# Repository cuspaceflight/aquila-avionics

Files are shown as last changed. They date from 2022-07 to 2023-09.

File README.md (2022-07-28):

# Aquila Avionics
Schematics and firmware for Aquila flight computer.

## Functions
* **Altimetry** - Accurately estimate altitude with barometer, GPS and accelerometer
* **Recovery** - Activate pyrotechnics to deploy parachute stages at appropriate points during descent
*  **Data logging** - Log altitude data and other parameters for post-flight analysis
* **Telemetry** - Transmit data to a ground station during flight as a backup should the vehicle be lost
* **Location** - Continually transmit location after landing to aid finding the vehicle

## Specifications
* **Mass** -  2kg
* **Acceleration** - 30g
* **Altitude** - 150km
* **Speed** - 1500m/s
* **Flexibility** - Exact flight and recovery profile is TBC
*  **Budget** - �150

# Overview
What follows here is a very brief overview of the design, broken down by component. It's aim is to familiarise the reader with what this project includes and some of the decisions made.
## Batteries
The computer is designed to run from two 18650 Li-Ions in series. A battery management chip monitors the cell voltages and automatically balances them if necessary. There is no onboard charger, so batteries must be charged separately before installation/flights. Ideally cells with built-in under-volt protection should be used. The battery holders are physically mounted to the board (but will be mechanically supported by additional hardware). Power can be switched on and off via a screw terminal.  To connect the batteries to the rest of the board, a jumper is secured between the two terminals. A potential divider allows the microcontroller to directly monitor the battery voltages.

Additionally, a 3V CR2032 type cell is mounted to the board. This maintains real time clocks in the microcontroller and GPS receiver, improving resilience against power cycle events during flight.
## Power supplies
The board has two power supplies: 3.3V 3A and 5V 3A. The 3.3V supply powers most of the electronics on the board and is permanently on. The 5V supply is dedicated to pyrotechnics and servos as required by the recovery system. It is switched on and off by the microcontroller to conserve power when not needed and as a safety layer. A terminal is provided for an external safety switch. When shorted, this terminal disables the pyro power supply, eliminating the risk of unintentionally activating pyrotechnics during any activities leading up to launch.
## Sensors
### Barometer
A barometer is mounted on the board to measure atmospheric pressure. This is particularly useful during descent to deploy parachute stages at appropriate altitudes close to the ground. The model used is a MS5611-01BA03. It has a resolution on the order of tenths of millibar, but a minimum pressure of 10 millibar limits it's usefulness to below 30 km altitude.
### GPS
A U-blox MAX-M8Q receiver is included for completeness. CoCom regulations limit the operation of civilian GPS chips faster than 1000 knots (~500 m/s) and above 18 km, both of which will be exceeded early in Griffin's flight profile. Therefore the GPS will not be relied on for navigational purposes, but purely for data collection. It may be the case that once the rocket slows below 1000 knots near apogee, a fix can once again be acquired. This is uncertain as the manufacturer does not specify behaviour at these extremes.

An additional Low-Noise Amplifier and band-pass filter are included in the signal path as antenna challenges and telemetry radio interference will degrade signal quality.
### Accelerometer
The most important sensor for navigation and apogee deployment is the accelerometer. An inertial navigation system will be implemented to estimate the vehicle's velocity and altitude based on accelerometer readings. The double integration of acceleration to velocity leads to errors on the order of time squared, so it is imperative the accelerometer readings are low noise and very stable. Combined with this requirement, a high g range is required as the rocket will accelerate at up to 30g at some points.  An Analog Devices ADXL357 is chosen. It boasts 20 bit resolution, ultra-low noise and high bias stability with a range of +/- 40g.
## Telemetry
An Si4463 radio transceiver provides a bi-directional radio link with a ground station. This will be useful for configuring the computer during launch preparations as well as backing up as much data as possible should the vehicle be lost. A secondary purpose for the radio will be locating the vehicle after a successful recovery. The current setup is designed for operation in the 915 MHz ISM band, subject to regulatory compliance.
## Interfaces
Connectors on the board include: 
* **female SMA** for GPS antenna
* **female SMA** for telemetry antenna
* **6-way Molex Nano-Fit** for a separate, remote, barometer, in case structural limitations prevent the avionics bay being vented to the atmosphere
* **6-way Molex Nano-Fit** for up to four servo motors
* **4x 2-way screw terminal** for up to four pyrotechnics
* **Micro USB** for programming and serial communication

The pyro channels can provide 5V at 1A continuous as limited by the FETs, 3A peak as limited by the power supply. They also include individual continuity measurement by draining approximately 50uA through the pyro.
## Microcontroller
A Teensy 4.1 was selected as the microcontroller. It is based around an ARM Cortex-M7 running at 600MHz. The first reason for this choice is that it includes many features we would only have to implement ourselves such as a real time clock, MicroSD storage, USB interface etc. Secondly, it is compatible with the Arduino ecosystem, granting access to many existing libraries and improving access to the firmware for CUSF members.
## Antennas
Antennas are an area of ongoing research, hence nothing has been included in this repo yet. Carbon-fibre reinforced polymer (CFRP) construction precludes antennas being mounted inside the rocket body, and extreme aerodynamic and aerothermal loads make any kind of protruding antenna impossible. This leaves the only possible solution as conformal patch antenna arrays. Methods to design and optimise these antennas and feed networks are currently being developed. See <https://github.com/cuspaceflight/aperture>.

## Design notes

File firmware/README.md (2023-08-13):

#### Important:
Copy the `aquila_interface` folder into your `Arduino/libraries` directory before compiling. If you wish to run Hardware-In-Loop (HIL) testing, also copy `aquila_hil_interface.h` and `aquila_hil_interface.cpp` into this libraries folder.

#### Guide to files
* aquila_flight - actual flight program
* aquila_interface - library for interacting with Aquila hardware
* individual_sensor_tests - a small program for each sensor, used to test protocols
* inertial_calibration - calculates two-point calibrations for accelerometers and gyroscopes by having you hold the board in different orientations
* sensor_dump - reads all sensors using aquila_interface and prints their values to serial

#### HIL Testing
To run an HIL test on the flight computer with imitated sensor readings from a simulated flight, uncomment the indicated line at the top of `aquila_flight.ino`. The "liftoff" will occur automatically 30 seconds after startup, so make sure to issue the "unlock" command within this time.

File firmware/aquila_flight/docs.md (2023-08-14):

# Aquila Flight Software Documentation

## Contents

**Requirement-to-Code Tracking**

**Hardware Interface**

**Design**

- System States
- Background Operations
- Serial Interface

## Requirement-to-Code Tracking

To ensure the software meets all high-level requirements and does not contain any unused code, sections of the requirements are linked to sections of the source code. These are indicated by square brackets containing a number. The source code is commented with corresponding numbers to indicate where these requirements are implemented. For example a requirement may say “When X is true, Y should occur \[42]” and the corresponding section of code will have a comment “// REQ\[42]”. Where a single section of code serves to implement several requirements, the comment contains all of them e.g. “// REQ\[42]\[45]\[51]”. These should be standalone comments at the beginning of blocks of code or at the end of specific lines.

## Hardware Interface

A library called ‘aquila\_interface’ has been written to interface with the sensors and peripherals on the board. This is bare-bones protocol level code, and does not have a set of formal requirements associated with it at this time.

## High-Level Requirements

The architecture of the Aquila Flight program comprises two types of code: mode based; and background. The system state represents the current stage of flight, with transitions occurring when specific conditions are met. The transition from one mode to another may be associated with one or more actions such as actuation of a vehicle system. Background functions are run repeatedly at set rates to update sensor readings or log data. Some background functions may run only when the system is in specific modes.

### System States

There are seven total flight stages, represented by a mode. \[1]

| **Num** | **Name** | **Criteria to enter** | **Actions** |
| --- | --- | --- | --- |
| 0 | LOCKED | Startup \[2], lock command received \[45] | Set altitude and velocity estimates to zero \[46] |
| 1 | PAD | unlock command received \[3] | |
| 2 | BURN | velocity > 10m/s \[4] | |
| 3 | COAST | acceleration < 0 \[5] | |
| 4 | APOGEE | velocity < 0 \[6] | Activate bottle burst pyro \[9] |
| 5 | DESCENT  | barometric altitude below 500m \[7] | Release parachute servos \[10] |
| 6 | LAND | Barometric pressure constant for 10 seconds \[8] | Reduce logging rate to 10Hz \[11], disarm pyros \[51] |

### Background Operations

| **Operation** | **Modes** | **Rate** | **Description** |
| --- | --- | --- | --- |
| Acceleration integration | all except LOCKED and LAND \[18] | \~1kHz\[24] | The ADXL357 raises an interrupt when it has a new reading. The handler updates the velocity and altitude estimates \[30]. When in PAD state, accelerations < 0.01g are discarded \[47]. |
| Sensor updates | All \[19] | 100Hz \[25] | All sensors are read and readings stored \[31] |
| Data logging | All \[20] | 100Hz\[26]  | Write all sensor readings and system parameters to SD card \[32] |
| Telemetry transmission | All \[21] | 10Hz\[27] | Transmit packet of sensor readings and system parameters over radio \[33] |
| Telecommand reception  | All \[21] | 10Hz\[27] | Receive command from radio \[52] |
| Serial write | LOCKED and PAD \[22] | 10Hz\[28] | Send sensor readings and system parameters over Serial \[34] |
| Serial read | LOCKED and PAD \[23] | 100Hz\[29]  | Read serial port for commands \[35] |

### Command Interface

Several commands can be sent to the vehicle either by the serial connection or via the radio. The commands currently implemented are as follows.

| **Command** | **Action** |
| --- | --- |
| N | Print system state to console \[36] |
| S | Start printing system state at a rate of 10Hz \[37] |
| P | Stop printing system state \[38] |
| L | Put system into LOCKED state and reset altitude and velocity \[39] |
| U | Put system into PAD state \[40] |
| V\* | Toggle servo position - LOCKED state only \[41] |
| A | Arm pyrotechnics \[42] |
| D | Disarm pyrotechnics \[43] |
| C | Calibrate launch pad barometric pressure \[49] |

\* requires pyrotechnics to be armed \[44]

### Recovery Safety

To prevent unintentional release of the spring loaded recovery system, the servos should be set to the latched position whenever the pyro channels are armed \[48].

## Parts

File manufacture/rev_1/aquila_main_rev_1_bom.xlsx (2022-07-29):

Item | Qty | Reference(s) | Value | LibPart | Footprint | Datasheet | DigiKey | Farnell | Mouser | RS
1 | 3 | C1, C2, C20 | 100p | aquila:C-cusf-kicad | Capacitor_SMD:C_0402_1005Metric |  |  | 1758969
2 | 3 | C3, C4, C18 | 100n | aquila:C-cusf-kicad | Capacitor_SMD:C_0402_1005Metric |  |  | 2320759
3 | 2 | C5, C6 | 22u | aquila:C-cusf-kicad | Capacitor_THT:CP_Radial_D6.3mm_P2.50mm |  |  | 9452710
4 | 2 | C7, C8 | 1u | aquila:C-cusf-kicad | Capacitor_SMD:C_0402_1005Metric |  |  | 2310531
5 | 2 | C9, C10 | 1000u | Device:C_Polarized_Small | Capacitor_THT:CP_Radial_D8.0mm_P3.50mm | https://www.farnell.com/datasheets/2820375.pdf |  | 2760327
6 | 1 | C11 | 3p | Strix:C | Capacitor_SMD:C_0402_1005Metric |  |  | 1758933
7 | 1 | C12 | 5p1 | Strix:C | Capacitor_SMD:C_0402_1005Metric |  |  | 2781439
8 | 1 | C13 | 1p2 | Strix:C | Capacitor_SMD:C_0402_1005Metric |  |  | 3369062
9 | 9 | C14, C16, C22, C23, C27, C28, C30, C32, C35 | 0u1 | aquila:C-cusf-kicad | Capacitor_SMD:C_0402_1005Metric |  |  | 2320759
10 | 1 | C15 | 6n8 | Strix:C | Capacitor_SMD:C_0402_1005Metric |  |  | 2627370
11 | 5 | C17, C29, C31, C33, C36 | 10u | aquila:C-cusf-kicad | Capacitor_SMD:C_0402_1005Metric |  |  | 3013332
12 | 2 | C19, C26 | 20p | aquila:C-cusf-kicad | Capacitor_SMD:C_0402_1005Metric |  |  | 1758948
13 | 2 | C21, C24 | 3p3 | Strix:C | Capacitor_SMD:C_0402_1005Metric |  |  | 2627406
14 | 1 | C25 | 0u33 | aquila:C-cusf-kicad | Capacitor_SMD:C_0402_1005Metric |  |  | 2627379
15 | 1 | C34 | 10n | aquila:C-cusf-kicad | Capacitor_SMD:C_0402_1005Metric |  |  | 1758926
16 | 1 | C37 | 2n2 | aquila:C-cusf-kicad | Capacitor_SMD:C_0402_1005Metric |  |  | 2320767
17 | 2 | D1, D2 | 1N5820 | Diode:1N5820 | Diode_THT:D_DO-201AD_P15.24mm_Horizontal | http://www.vishay.com/docs/88526/1n5820.pdf |  | 2317410
18 | 1 | D3 | GREEN | Device:LED_Small | Diode_SMD:D_0603_1608Metric | ~ |  | 3796304
19 | 1 | D4 | RED | Device:LED_Small | Diode_SMD:D_0603_1608Metric | ~ |  | 3796306
20 | 2 | D5, D6 | D_TVS | aquila:D_TVS | Diode_SMD:D_0402_1005Metric |  |  | 2368169
21 | 10 | H1, H2, H3, H4, H5, H6, H7, H8, H9, H10 | M3 | Mechanical:MountingHole_Pad | MountingHole:MountingHole_3.2mm_M3_DIN965_Pad | ~
22 | 1 | IC1 | MS5611-01BA03 | aquila:MS5611-01BA03 | aquila:MS5611 |  |  | 2362662
23 | 1 | J1 | 120591-1 | aquila:120591-1 | aquila:120591-1 | https://www.farnell.com/cad/1815976.pdf | A99328-ND
24 | 2 | J2, J3 | 1042 | aquila:1043P | aquila:1042 |  | 36-1042P-ND
25 | 1 | J4 | PWR | Connector:Screw_Terminal_01x02 | aquila:MP_2.54_screw_terminal_2x1 | ~ |  | 3817460
26 | 1 | J5 | TELEM | Connector:Conn_Coaxial | aquila:SMA_VERT | https://www.mouser.co.uk/datasheet/2/398/PCB.SMAFST.J.A.HT-26997.pdf |  |  | 960-PCB.SMAFST.J.AHT
27 | 1 | J6 | GPS | Connector:Conn_Coaxial | aquila:SMA_VERT | https://www.mouser.co.uk/datasheet/2/398/PCB.SMAFST.J.A.HT-26997.pdf |  |  | 960-PCB.SMAFST.J.AHT
28 | 1 | J7 | BARO | Connector:Conn_01x06_Male | aquila:molex_nano_fit_x6_105310-1106 | https://www.molex.com/pdm_docs/sd/1053101106_sd.pdf | WM16880-ND | 2820682
29 | 1 | J8 | BMI-S-201 | aquila:BMI-S-201 | aquila:BMI-S-201 | ~ |  | 2497715 | ~ | ~
30 | 1 | J9 | PYRO_1 | Connector:Screw_Terminal_01x02 | aquila:MP_2.54_screw_terminal_2x1 | ~ |  | 3817460
31 | 1 | J10 | PYRO_3 | Connector:Screw_Terminal_01x02 | aquila:MP_2.54_screw_terminal_2x1 | ~ |  | 3817460
32 | 1 | J11 | PYRO_2 | Connector:Screw_Terminal_01x02 | aquila:MP_2.54_screw_terminal_2x1 | ~ |  | 3817460
33 | 1 | J12 | PYRO_4 | Connector:Screw_Terminal_01x02 | aquila:MP_2.54_screw_terminal_2x1 | ~ |  | 3817460
34 | 1 | J13 | PYRO_SAFE | Connector:Screw_Terminal_01x02 | aquila:MP_2.54_screw_terminal_2x1 | ~ |  | 3817460
35 | 1 | J14 | SERVO | Connector:Conn_01x06_Male | aquila:molex_nano_fit_x6_105310-1106 | https://www.molex.com/pdm_docs/sd/1053101106_sd.pdf | WM16880-ND | 2820682
36 | 2 | L1, L2 | 100u | aquila:L-cusf-kicad | aquila:L_MP0028_124_125_127 | https://www.farnell.com/datasheets/3486014.pdf |  | 2288307
37 | 1 | L3 | 120n | Strix:L | Inductor_SMD:L_0402_1005Metric |  |  | 3471254
38 | 1 | L4 | 18n | Strix:L | Inductor_SMD:L_0402_1005Metric |  |  | 1343084
39 | 1 | L5 | 3n3 | Strix:L | Inductor_SMD:L_0402_1005Metric |  |  | 1343068
40 | 2 | L6, L8 | 24n | Strix:L | Inductor_SMD:L_0402_1005Metric |  |  | 3263549
41 | 2 | L7, L9 | 12n | Strix:L | Inductor_SMD:L_0402_1005Metric |  |  | 1343082
42 | 2 | NT1, NT2 | Tie_2 | Device:NetTie_2 | NetTie:NetTie-2_THT_Pad1.0mm | ~
43 | 1 | NT3 | NetTie_2 | Device:NetTie_2 | NetTie:NetTie-2_SMD_Pad0.5mm | ~
44 | 4 | Q1, Q2, Q3, Q4 | IRF7509PbF | :IRF7509PbF_6 | aquila:IRF7509PbF | https://www.farnell.com/datasheets/138074.pdf |  | 1611421
45 | 10 | R1, R22, R23, R24, R25, R26, R33, R34, R35, R36 | 10k | aquila:R-cusf-kicad | Resistor_SMD:R_0402_1005Metric |  |  | 2072517
46 | 8 | R2, R6, R7, R9, R15, R16, R19, R20 | DNP | aquila:R-cusf-kicad | Resistor_SMD:R_0402_1005Metric
47 | 4 | R3, R12, R13, R14 | 100 | aquila:R-cusf-kicad | Resistor_SMD:R_0402_1005Metric |  |  | 2072515
48 | 1 | R4 | 330 | aquila:R-cusf-kicad | Resistor_SMD:R_0402_1005Metric |  |  | 2074057
49 | 4 | R5, R8, R17, R18 | 0 | aquila:R-cusf-kicad | Resistor_SMD:R_0402_1005Metric
50 | 2 | R10, R11 | 160 | aquila:R-cusf-kicad | Resistor_SMD:R_0402_1005Metric |  |  | 2072673
51 | 1 | R21 | 20k | aquila:R-cusf-kicad | Resistor_SMD:R_0402_1005Metric |  |  | 2072753
52 | 8 | R27, R28, R29, R30, R39, R40, R41, R42 | 100k | aquila:R-cusf-kicad | Resistor_SMD:R_0402_1005Metric |  |  | 2072519
53 | 4 | R31, R32, R43, R44 | 200k | aquila:R-cusf-kicad | Resistor_SMD:R_0402_1005Metric |  |  | 2072758
54 | 3 | R37, R38, R45 | 4k7 | aquila:R-cusf-kicad | Resistor_SMD:R_0402_1005Metric |  |  | 2073064
55 | 35 | TP1, TP2, TP3, TP4, TP5, TP6, TP7, TP8, TP9, TP10, TP11, TP12, TP13, TP14, TP15, TP16, TP17, TP18, TP19, TP20, TP21, TP22, TP23, TP24, TP25, TP26, TP27, TP28, TP29, TP30, TP31, TP32, TP33, TP34, TP35 | TestPoint | Connector:TestPoint | TestPoint:TestPoint_Pad_D1.0mm | ~
56 | 1 | U1 | LM2576S-3.3/NOPB | aquila:LM2576S-3.3{slash}NOPB | aquila:TO-236_5 | https://www.ti.com/lit/ds/symlink/lm2576.pdf |  | 3008143
57 | 1 | U2 | LM2576D2TR4-5G | aquila:LM2576S-3.3{slash}NOPB | aquila:TO-236_5 | https://www.farnell.com/datasheets/5904.pdf |  | 2534166
58 | 1 | U3 | MAX-M8Q | RF_GPS:MAX-M8Q | aquila:MAX-M8Q | https://www.u-blox.com/sites/default/files/MAX-M8-FW3_DataSheet_%28UBX-15031506%29.pdf
59 | 1 | U4 | Si4463 | RF:Si4463 | Package_DFN_QFN:QFN-20-1EP_4x4mm_P0.5mm_EP2.6x2.6mm_ThermalVias | https://www.silabs.com/documents/public/data-sheets/Si4464-63-61-60.pdf | 336-4346-1-ND
60 | 1 | U5 | B3520 | aquila:B3520 | aquila:B3520 | https://media.digikey.com/pdf/Data%20Sheets/Epcos%20PDFs/B39162B3520U410.pdf | 495-2363-1-ND
61 | 1 | U6 | SKY65723-11 | aquila:SKY65723-11 | aquila:SKY65723-81 | https://www.skyworksinc.com/-/media/SkyWorks/Documents/Products/2801-2900/SKY65723_11_203921F.pdf |  |  | 873-SKY65723-81
62 | 1 | U7 | ADXL357 | aquila:ADXL357 | aquila:ADXL357 |  | 505-ADXL357BEZ-ND
63 | 1 | U8 | BQ29200 | aquila:BQ29200 | aquila:VSOP-8 | https://www.ti.com/lit/ds/symlink/bq29200.pdf?ts=1647814951091 |  | 2383074
64 | 1 | U9 | Teensy4.1 | teensy:Teensy4.1 | teensy:Teensy41 |  | 223-1622-1-ND
65 | 1 | U10 | MPU-6050 | Sensor_Motion:MPU-6050 | Sensor_Motion:InvenSense_QFN-24_4x4mm_P0.5mm | https://store.invensense.com/datasheets/invensense/MPU-6050_DataSheet_V3%204.pdf |  | 3769961
66 | 1 | Y1 | 30M | Device:Crystal_GND2_Small | aquila:crystal_ABM8 | https://www.farnell.com/datasheets/2792510.pdf |  | 3228351

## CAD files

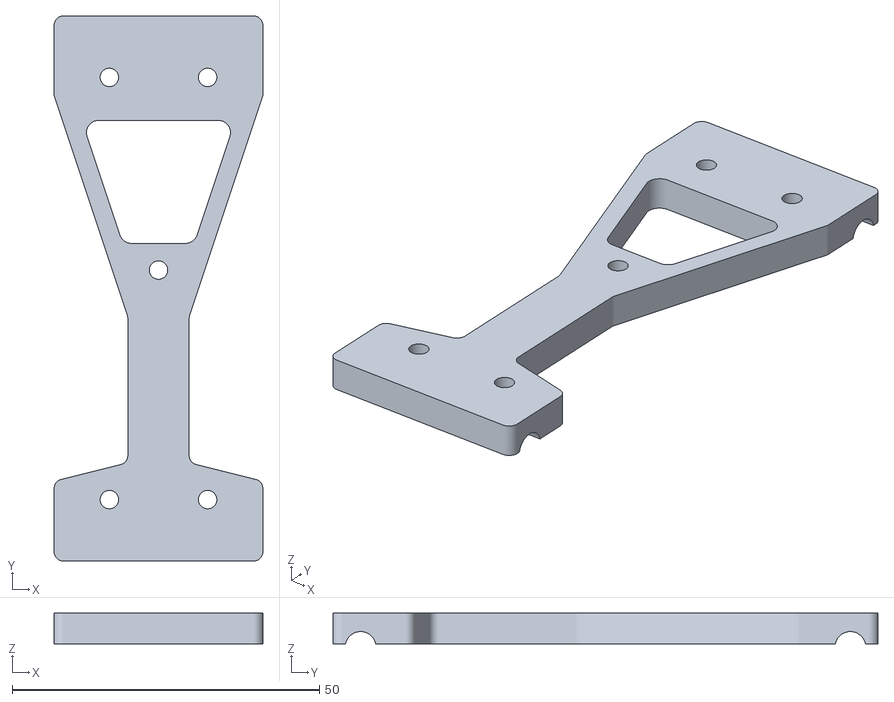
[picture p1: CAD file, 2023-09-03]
mounting/rfm95w_mount-top.stl
34.0 x 88.8 x 5.00

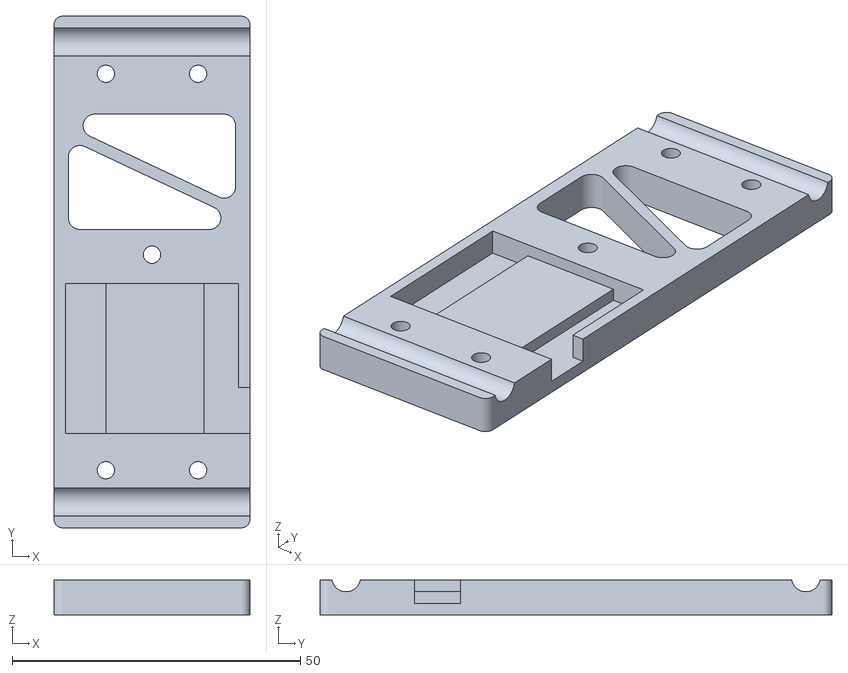
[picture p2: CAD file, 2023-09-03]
mounting/rfm95w_mount-base.stl
34.0 x 88.8 x 6.00

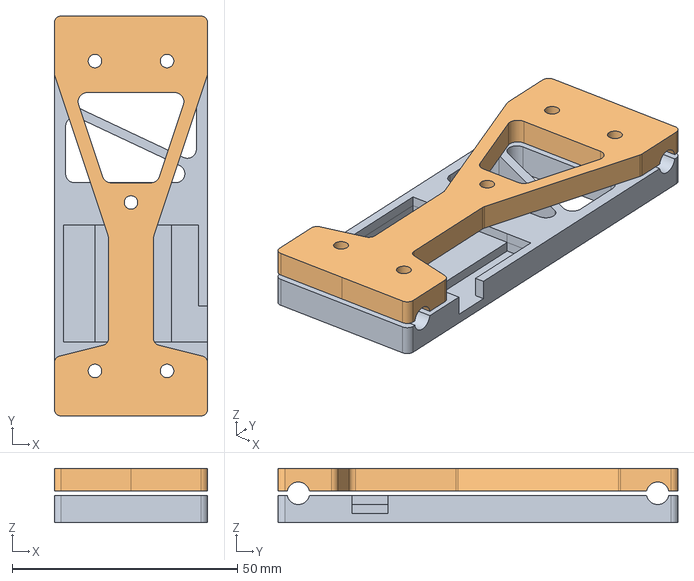
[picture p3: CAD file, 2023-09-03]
mounting/rfm95w_mount.FCStd
34.0 x 88.8 x 12.0 mm

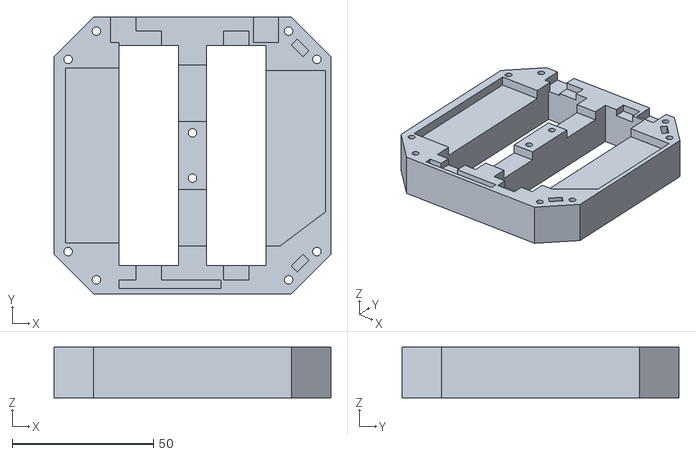
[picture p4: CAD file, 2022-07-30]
mounting/support-PartBody.stl
98.0 x 98.0 x 18.0

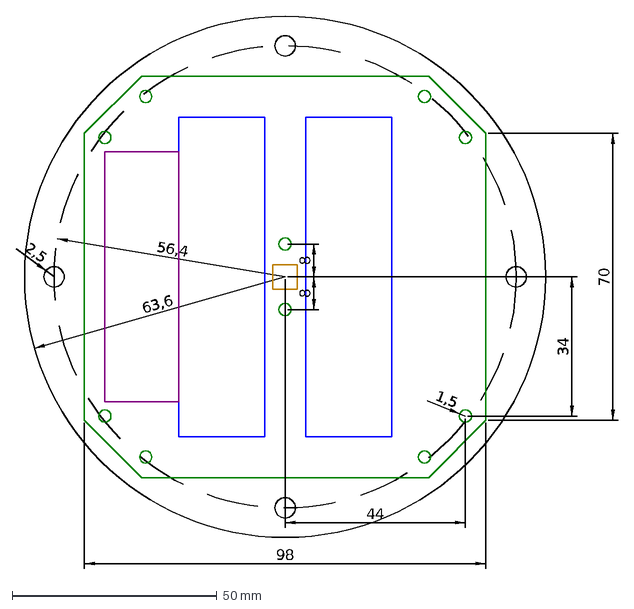
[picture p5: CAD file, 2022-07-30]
mounting/#flange.dxf
63,6
56,4
98
70
2,5
8
44
34
1,5

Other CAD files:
mounting/support.FCStd
mounting/flange.dxf

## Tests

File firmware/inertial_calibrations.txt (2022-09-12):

----- ADXL357 -----
x sensitivity: 12535.15
x offset: 64.44
y sensitivity: 12622.60
y offset: 163.36
z sensitivity: 12157.37
z offset: 1270.68
----- MPU6050 Acceleromter -----
x sensitivity: 2045.54
x offset: 147.62
y sensitivity: 2048.25
y offset: -31.73
z sensitivity: 2099.57
z offset: -51.80
----- MPU6050 Gyroscopes -----
x offset: -51.39
y offset: -21.91
z offset: 1.77
All offsets in LSB, accelerometer sensitivities in LSB /g

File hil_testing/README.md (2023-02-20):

#### HIL Testing
These files are used to generate code for HIL testing. The CSV file contains data from a flight simulation by B. Wardell: https://github.com/Barty129/Uncarved-Block/. The Python program converts this data to an interpolating function in C++ code, so that it can be directly pasted into aquila_hil_interface.cpp.

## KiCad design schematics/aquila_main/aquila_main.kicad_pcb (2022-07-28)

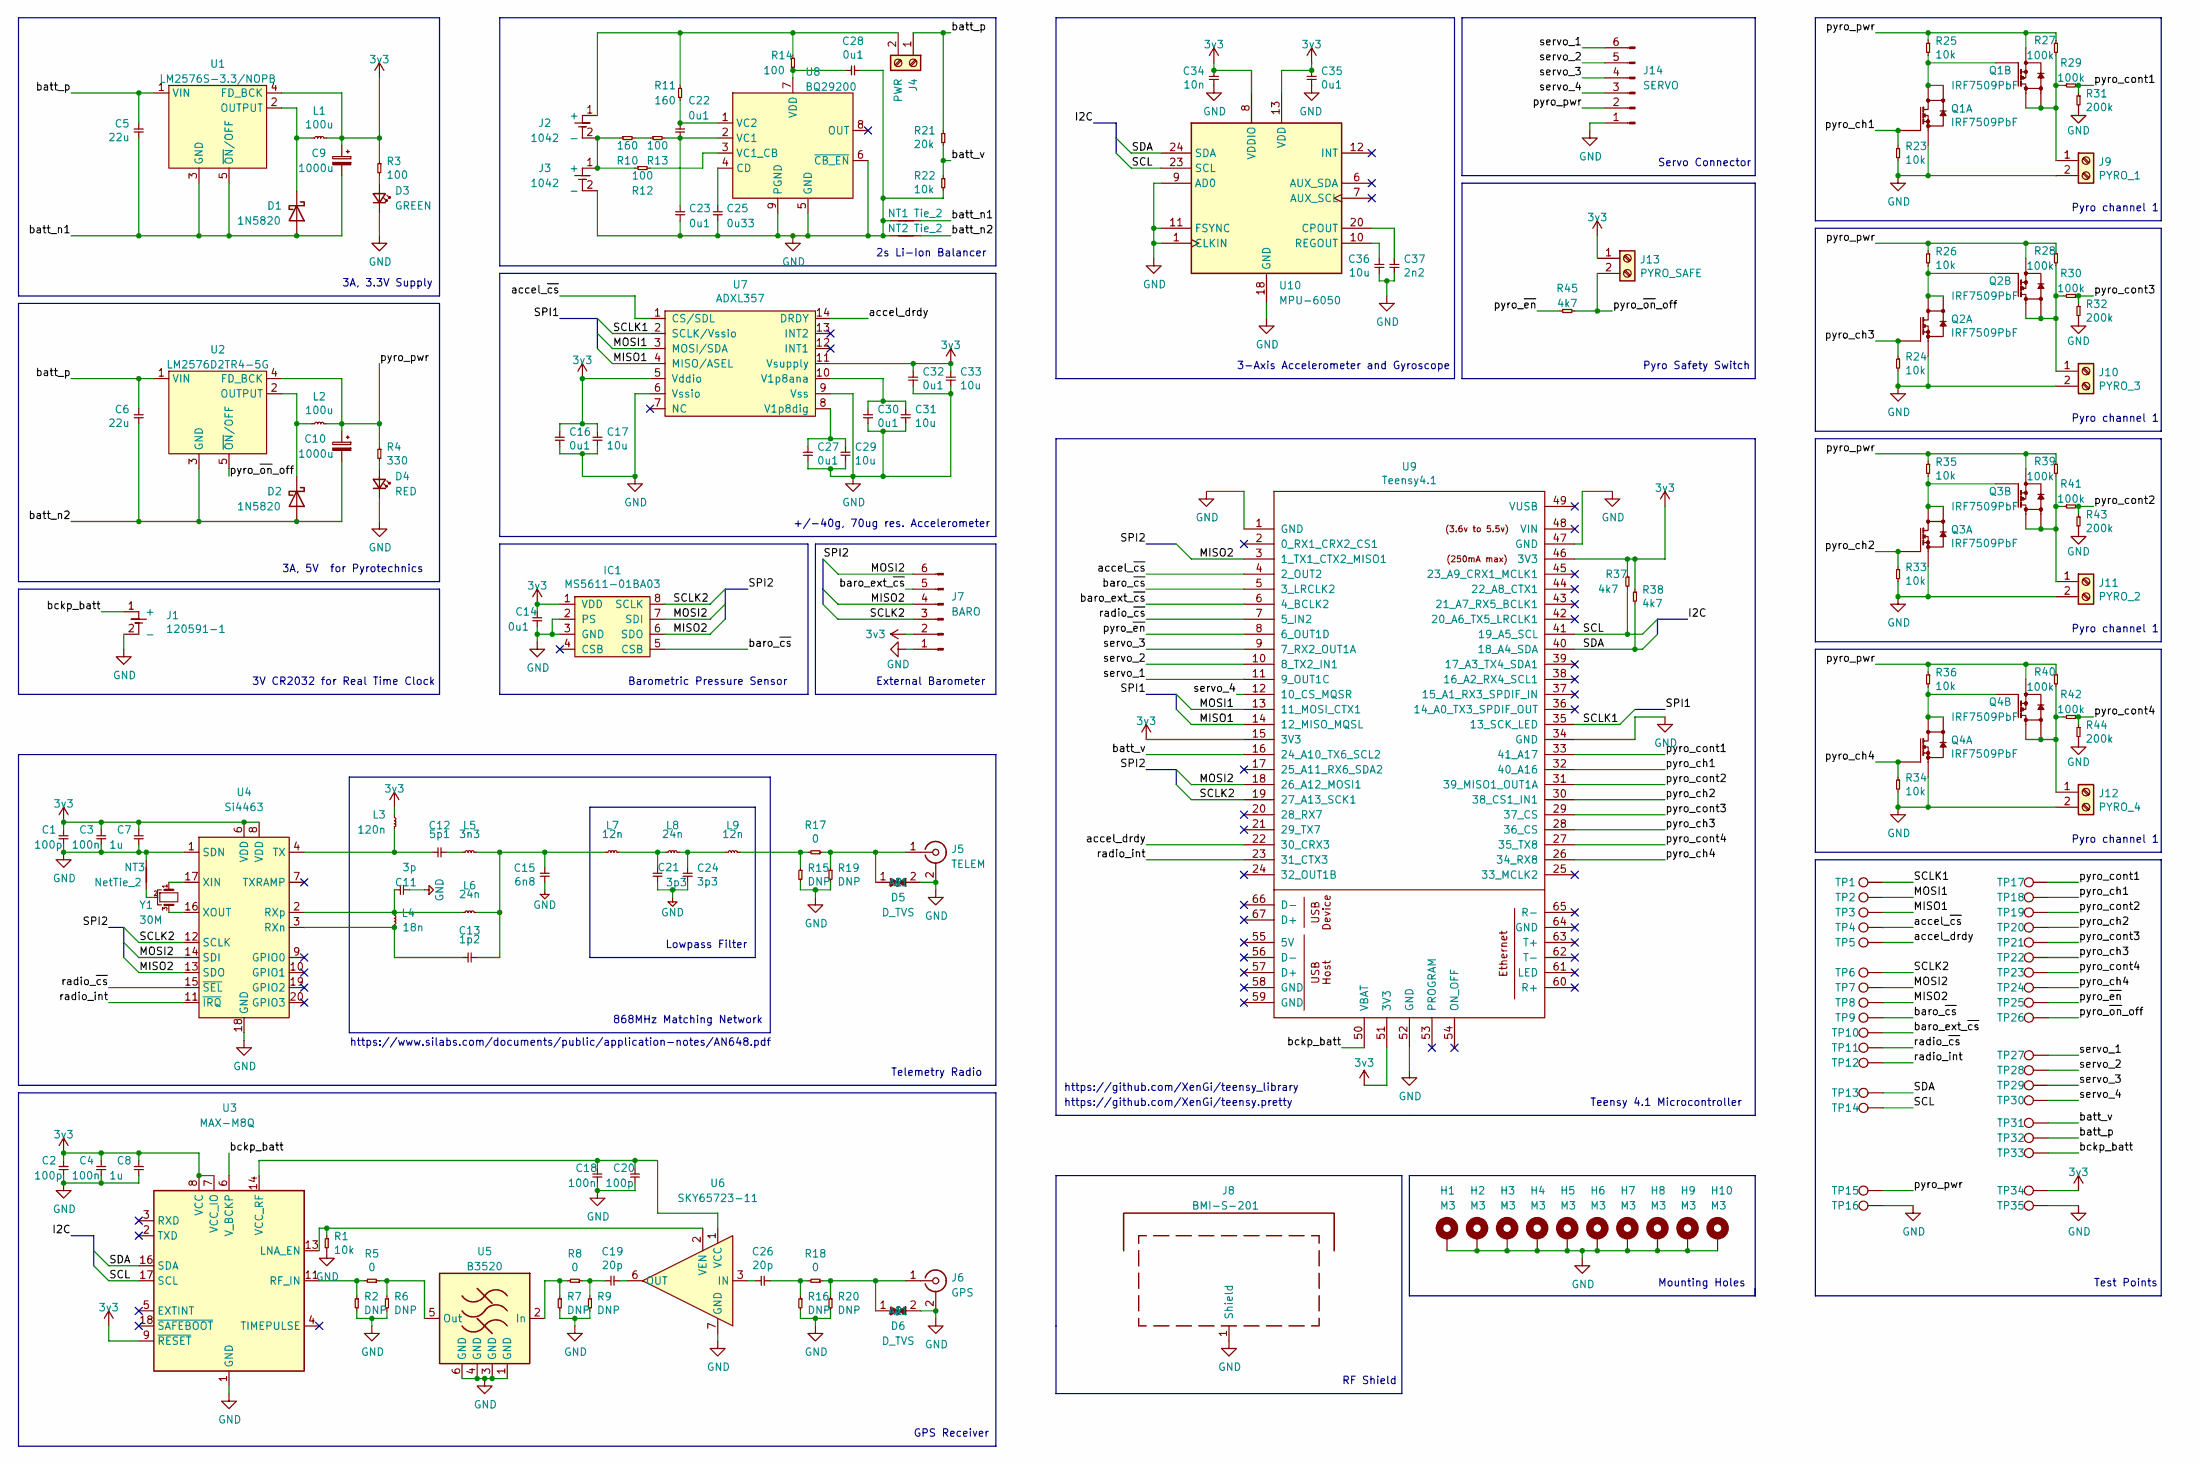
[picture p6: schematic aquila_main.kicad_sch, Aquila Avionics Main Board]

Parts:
C1, C2, C20: 100p; C_0402_1005Metric
C3, C4, C18: 100n; C_0402_1005Metric
C5, C6: 22u; CP_Radial_D6.3mm_P2.50mm; Farnell 9452710
C7, C8: 1u; C_0402_1005Metric
C9, C10: 1000u; CP_Radial_D8.0mm_P3.50mm; Farnell 2760327
C11: 3p; C_0402_1005Metric; Farnell 1758933
C12: 5p1; C_0402_1005Metric; Farnell 2781439
C13: 1p2; C_0402_1005Metric; Farnell 3369062
C14, C16, C22, C23, C27, C28, C30, C32, C35: 0u1; C_0402_1005Metric
C15: 6n8; C_0402_1005Metric; Farnell 2627370
C17, C29, C31, C33, C36: 10u; C_0402_1005Metric
C19, C26: 20p; C_0402_1005Metric
C21, C24: 3p3; C_0402_1005Metric; Farnell 2627406
C25: 0u33; C_0402_1005Metric
C34: 10n; C_0402_1005Metric
C37: 2n2; C_0402_1005Metric
D1, D2: 1N5820; D_DO-201AD_P15.24mm_Horizontal; Farnell 2317410
D3: GREEN; D_0603_1608Metric; Farnell 3796304
D4: RED; D_0603_1608Metric; Farnell 3796306
D5, D6: D_TVS; D_0402_1005Metric; Farnell 2368169
H1, H2, H3, H4, H5, H6, H7, H8, H9, H10: M3; MountingHole_3.2mm_M3_DIN965_Pad
IC1: MS5611-01BA03; MS5611; Farnell 2362662
J1: 120591-1; DigiKey A99328-ND
J2, J3: 1042; DigiKey 36-1042P-ND
J4: PWR; MP_2.54_screw_terminal_2x1; Farnell 3817460
J5: TELEM; SMA_VERT; Mouser 960-PCB.SMAFST.J.AHT
J6: GPS; SMA_VERT; Mouser 960-PCB.SMAFST.J.AHT
J7: BARO; molex_nano_fit_x6_105310-1106; Farnell 2820682
J8: BMI-S-201; Farnell 2497715
J9: PYRO_1; MP_2.54_screw_terminal_2x1; Farnell 3817460
J10: PYRO_3; MP_2.54_screw_terminal_2x1; Farnell 3817460
J11: PYRO_2; MP_2.54_screw_terminal_2x1; Farnell 3817460
J12: PYRO_4; MP_2.54_screw_terminal_2x1; Farnell 3817460
J13: PYRO_SAFE; MP_2.54_screw_terminal_2x1; Farnell 3817460
J14: SERVO; molex_nano_fit_x6_105310-1106; Farnell 2820682
L1, L2: 100u; L_MP0028_124_125_127; Farnell 2288307
L3: 120n; L_0402_1005Metric; Farnell 3471254
L4: 18n; L_0402_1005Metric; Farnell 1343084
L5: 3n3; L_0402_1005Metric; Farnell 1343068
L6, L8: 24n; L_0402_1005Metric; Farnell 3263549
L7, L9: 12n; L_0402_1005Metric; Farnell 1343082
NT1, NT2: Tie_2; NetTie-2_THT_Pad1.0mm
NT3: NetTie_2; NetTie-2_SMD_Pad0.5mm
Q1, Q2, Q3, Q4: IRF7509PbF; Farnell 1611421
R1, R22, R23, R24, R25, R26, R33, R34, R35, R36: 10k; R_0402_1005Metric
R2, R6, R7, R9, R15, R16, R19, R20: DNP; R_0402_1005Metric
R3, R12, R13, R14: 100; R_0402_1005Metric
R4: 330; R_0402_1005Metric
R5, R8, R17, R18: 0; R_0402_1005Metric
R10, R11: 160; R_0402_1005Metric
R21: 20k; R_0402_1005Metric
R27, R28, R29, R30, R39, R40, R41, R42: 100k; R_0402_1005Metric
R31, R32, R43, R44: 200k; R_0402_1005Metric
R37, R38, R45: 4k7; R_0402_1005Metric
TP1, TP2, TP3, TP4, TP5, TP6, TP7, TP8, TP9, TP10, TP11, TP12, TP13, TP14, TP15, TP16, TP17, TP18, TP19, TP20, TP21, TP22, TP23, TP24, TP25, TP26, TP27, TP28, TP29, TP30, TP31, TP32, TP33, TP34, TP35: TestPoint; TestPoint_Pad_D1.0mm
U1: LM2576S-3.3/NOPB; TO-236_5; Farnell 3008143
U2: LM2576D2TR4-5G; TO-236_5; Farnell 2534166
U3: MAX-M8Q
U4: Si4463; QFN-20-1EP_4x4mm_P0.5mm_EP2.6x2.6mm_ThermalVias; DigiKey 336-4346-1-ND
U5: B3520; DigiKey 495-2363-1-ND
U6: SKY65723-11; SKY65723-81; Mouser 873-SKY65723-81
U7: ADXL357; DigiKey 505-ADXL357BEZ-ND
U8: BQ29200; VSOP-8; Farnell 2383074
U9: Teensy4.1; Teensy41; DigiKey 223-1622-1-ND
U10: MPU-6050; InvenSense_QFN-24_4x4mm_P0.5mm; Farnell 3769961
Y1: 30M; crystal_ABM8; Farnell 3228351

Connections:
+3V3: C1.1, C2.1, C3.1, C4.1, C7.1, C8.1, C9.1, C14.1, C16.1, C17.1, C32.1, C33.1, C34.1, C35.1, IC1.1 (VDD), J7.2, J13.1, L1.2, L3.1, R3.1, R37.1, R38.1, TP34.1, U1.4 (FD_BCK), U3.7 (VCC_IO), U3.8 (VCC), U3.9 (~RESET), U4.6 (VDD), U4.8 (VDD), U7.5 (Vddio), U7.11 (Vsupply), U9.15 (3V3), U9.46 (3V3), U9.51 (3V3), U10.8 (VDDIO), U10.13 (VDD)
/MISO1: TP3.1, U7.4 (MISO/ASEL), U9.14 (12_MISO_MQSL)
/MISO2: IC1.6 (SDO), J7.4, TP8.1, U4.13 (SDO), U9.3 (1_TX1_CTX2_MISO1)
/MOSI1: TP2.1, U7.3 (MOSI/SDA), U9.13 (11_MOSI_CTX1)
/MOSI2: IC1.7 (SDI), J7.6, TP7.1, U4.14 (SDI), U9.18 (26_A12_MOSI1)
/SCL: R37.2, TP14.1, U3.17 (SCL), U9.41 (19_A5_SCL), U10.23 (SCL)
/SCLK1: TP1.1, U7.2 (SCLK/Vssio), U9.35 (13_SCK_LED)
/SCLK2: IC1.8 (SCLK), J7.3, TP6.1, U4.12 (SCLK), U9.19 (27_A13_SCK1)
/SDA: R38.2, TP13.1, U3.16 (SDA), U9.40 (18_A4_SDA), U10.24 (SDA)
/accel_drdy: TP5.1, U7.14 (DRDY), U9.22 (30_CRX3)
/accel_~cs: TP4.1, U7.1 (CS/SDL), U9.4 (2_OUT2)
/baro_ext_~cs: J7.5, TP10.1, U9.6 (4_BCLK2)
/baro_~cs: IC1.5 (CSB), TP9.1, U9.5 (3_LRCLK2)
/batt_n1: C5.2, C9.2, D1.2 (A), NT1.2, U1.3 (GND), U1.5 (~ON/OFF)
/batt_n2: C6.2, C10.2, D2.2 (A), NT2.2, U2.3 (GND)
/batt_p: C5.1, C6.1, J4.1, R21.1, TP32.1, U1.1 (VIN), U2.1 (VIN)
/batt_v: R21.2, R22.1, TP31.1, U9.16 (24_A10_TX6_SCL2)
/bckp_batt: J1.1 (+), TP33.1, U3.6 (V_BCKP), U9.50 (VBAT)
/pyro_ch1: Q1.2 (G1), R23.1, TP18.1, U9.32 (40_A16)
/pyro_ch2: Q3.2 (G1), R33.1, TP20.1, U9.30 (38_CS1_IN1)
/pyro_ch3: Q2.2 (G1), R24.1, TP22.1, U9.28 (36_CS)
/pyro_ch4: Q4.2 (G1), R34.1, TP24.1, U9.26 (34_RX8)
/pyro_cont1: R29.2, R31.1, TP17.1, U9.33 (41_A17)
/pyro_cont2: R41.2, R43.1, TP19.1, U9.31 (39_MISO1_OUT1A)
/pyro_cont3: R30.2, R32.1, TP21.1, U9.29 (37_CS)
/pyro_cont4: R42.2, R44.1, TP23.1, U9.27 (35_TX8)
/pyro_pwr: C10.1, J14.2, L2.2, Q1.3 (S2), Q2.3 (S2), Q3.3 (S2), Q4.3 (S2), R4.1, R25.1, R26.1, R27.1, R28.1, R35.1, R36.1, R39.1, R40.1, TP15.1, U2.4 (FD_BCK)
/pyro_~en: R45.1, TP25.1, U9.8 (6_OUT1D)
/pyro_~on_off: J13.2, R45.2, TP26.1, U2.5 (~ON/OFF)
/radio_int: TP12.1, U4.11 (~IRQ), U9.23 (31_CTX3)
/radio_~cs: TP11.1, U4.15 (~SEL), U9.7 (5_IN2)
/servo_1: J14.6, TP27.1, U9.11 (9_OUT1C)
/servo_2: J14.5, TP28.1, U9.10 (8_TX2_IN1)
/servo_3: J14.4, TP29.1, U9.9 (7_RX2_OUT1A)
/servo_4: J14.3, TP30.1, U9.12 (10_CS_MQSR)
GND: C1.2, C2.2, C3.2, C4.2, C7.2, C8.2, C11.2, C14.2, C15.2, C16.2, C17.2, C18.2, C20.2, C21.2, C23.1, C24.2, C25.1, C27.2, C28.2, C29.2, C30.2, C31.2, C32.2, C33.2, C34.2, C35.2, C36.2, C37.2, D3.1 (K), D4.1 (K), D5.2 (A2), D6.2 (A2), H1.1, H2.1, H3.1, H4.1, H5.1, H6.1, H7.1, H8.1, H9.1, H10.1, IC1.2 (PS), IC1.3 (GND), J1.2 (-), J3.2 (-), J5.2 (Ext), J6.2 (Ext), J7.1, J8.1 (Shield), J9.2, J10.2, J11.2, J12.2, J14.1, NT1.1, NT2.1, NT3.2, Q1.1 (S1), Q2.1 (S1), Q3.1 (S1), Q4.1 (S1), R1.2, R2.2, R6.2, R7.2, R9.2, R15.2, R16.2, R19.2, R20.2, R22.2, R23.2, R24.2, R31.2, R32.2, R33.2, R34.2, R43.2, R44.2, TP16.1, TP35.1, U3.1 (GND), U3.10 (GND), U3.12 (GND), U4.1 (SDN), U4.18 (GND), U4.21 (GND), U5.1 (GND), U5.3 (GND), U5.4 (GND), U5.6 (GND), U6.7 (GND), U7.6 (Vssio), U7.9 (Vss), U8.5 (GND), U8.6 (~CB_EN), U8.9 (PGND), U9.1 (GND), U9.34 (GND), U9.47 (GND), U9.52 (GND), U10.1 (CLKIN), U10.9 (AD0), U10.11 (FSYNC), U10.18 (GND)
unnamed: C11.1, L4.1, L6.1, U4.2 (RXp)
unnamed: C12.1, L3.2, U4.4 (TX)
unnamed: C12.2, L5.1
unnamed: C13.1, L4.2, U4.3 (RXn)
unnamed: C13.2, C15.1, L5.2, L6.2, L7.1
unnamed: C18.1, C20.1, U3.14 (VCC_RF), U6.1 (VCC)
unnamed: C19.1, R8.1, R9.1
unnamed: C19.2, U6.6 (OUT)
unnamed: C21.1, L7.2, L8.1
unnamed: C22.1, C23.2, R13.2, U8.2 (VC1)
unnamed: C22.2, R11.1, U8.1 (VC2)
unnamed: C24.1, L8.2, L9.1
unnamed: C25.2, U8.4 (CD)
unnamed: C26.1, U6.3 (IN)
unnamed: C26.2, R16.1, R18.2
unnamed: C27.1, C29.1, U7.8 (V1p8dig)
unnamed: C28.1, R14.1, U8.7 (VDD)
unnamed: C30.1, C31.1, U7.10 (V1p8ana)
unnamed: C36.1, U10.10 (REGOUT)
unnamed: C37.1, U10.20 (CPOUT)
unnamed: D1.1 (K), L1.1, U1.2 (OUTPUT)
unnamed: D2.1 (K), L2.1, U2.2 (OUTPUT)
unnamed: D3.2 (A), R3.2
unnamed: D4.2 (A), R4.2
unnamed: D5.1 (A1), J5.1 (In), R17.1, R19.1
unnamed: D6.1 (A1), J6.1 (In), R18.1, R20.1
unnamed: J2.1 (+), J4.2, R11.2, R14.2
unnamed: J2.2 (-), J3.1 (+), R10.1, R12.1
unnamed: J9.1, Q1.5 (D2), Q1.6 (D2), R27.2, R29.1
unnamed: J10.1, Q2.5 (D2), Q2.6 (D2), R28.2, R30.1
unnamed: J11.1, Q3.5 (D2), Q3.6 (D2), R39.2, R41.1
unnamed: J12.1, Q4.5 (D2), Q4.6 (D2), R40.2, R42.1
unnamed: L9.2, R15.1, R17.2
unnamed: Q1.4 (G2), Q1.7 (D1), Q1.8 (D1), R25.2
unnamed: Q2.4 (G2), Q2.7 (D1), Q2.8 (D1), R26.2
unnamed: Q3.4 (G2), Q3.7 (D1), Q3.8 (D1), R35.2
unnamed: Q4.4 (G2), Q4.7 (D1), Q4.8 (D1), R36.2
unnamed: R1.1, U3.13 (LNA_EN), U6.2 (VEN)
unnamed: R2.1, R5.2, U3.11 (RF_IN)
unnamed: R5.1, R6.1, U5.5 (Out)
unnamed: R7.1, R8.2, U5.2 (In)
unnamed: R10.2, R13.1
unnamed: R12.2, U8.3 (VC1_CB)
unnamed: U4.16 (XOUT), Y1.3
unnamed: U4.17 (XIN), Y1.1
unnamed: NT3.1, Y1.2

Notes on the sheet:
Pyro channel 1
Barometric Pressure Sensor
Telemetry Radio
Test Points
Mounting Holes
GPS Receiver
Teensy 4.1 Microcontroller
https://www.silabs.com/documents/public/application-notes/AN648.pdf
External Barometer
+/-40g, 70ug res. Accelerometer
https://github.com/XenGi/teensy_library
3-Axis Accelerometer and Gyroscope
Servo Connector
3A, 5V for Pyrotechnics
RF Shield
3V CR2032 for Real Time Clock
2s Li-Ion Balancer
868MHz Matching Network
Lowpass Filter
https://github.com/XenGi/teensy.pretty
Pyro Safety Switch
3A, 3.3V Supply

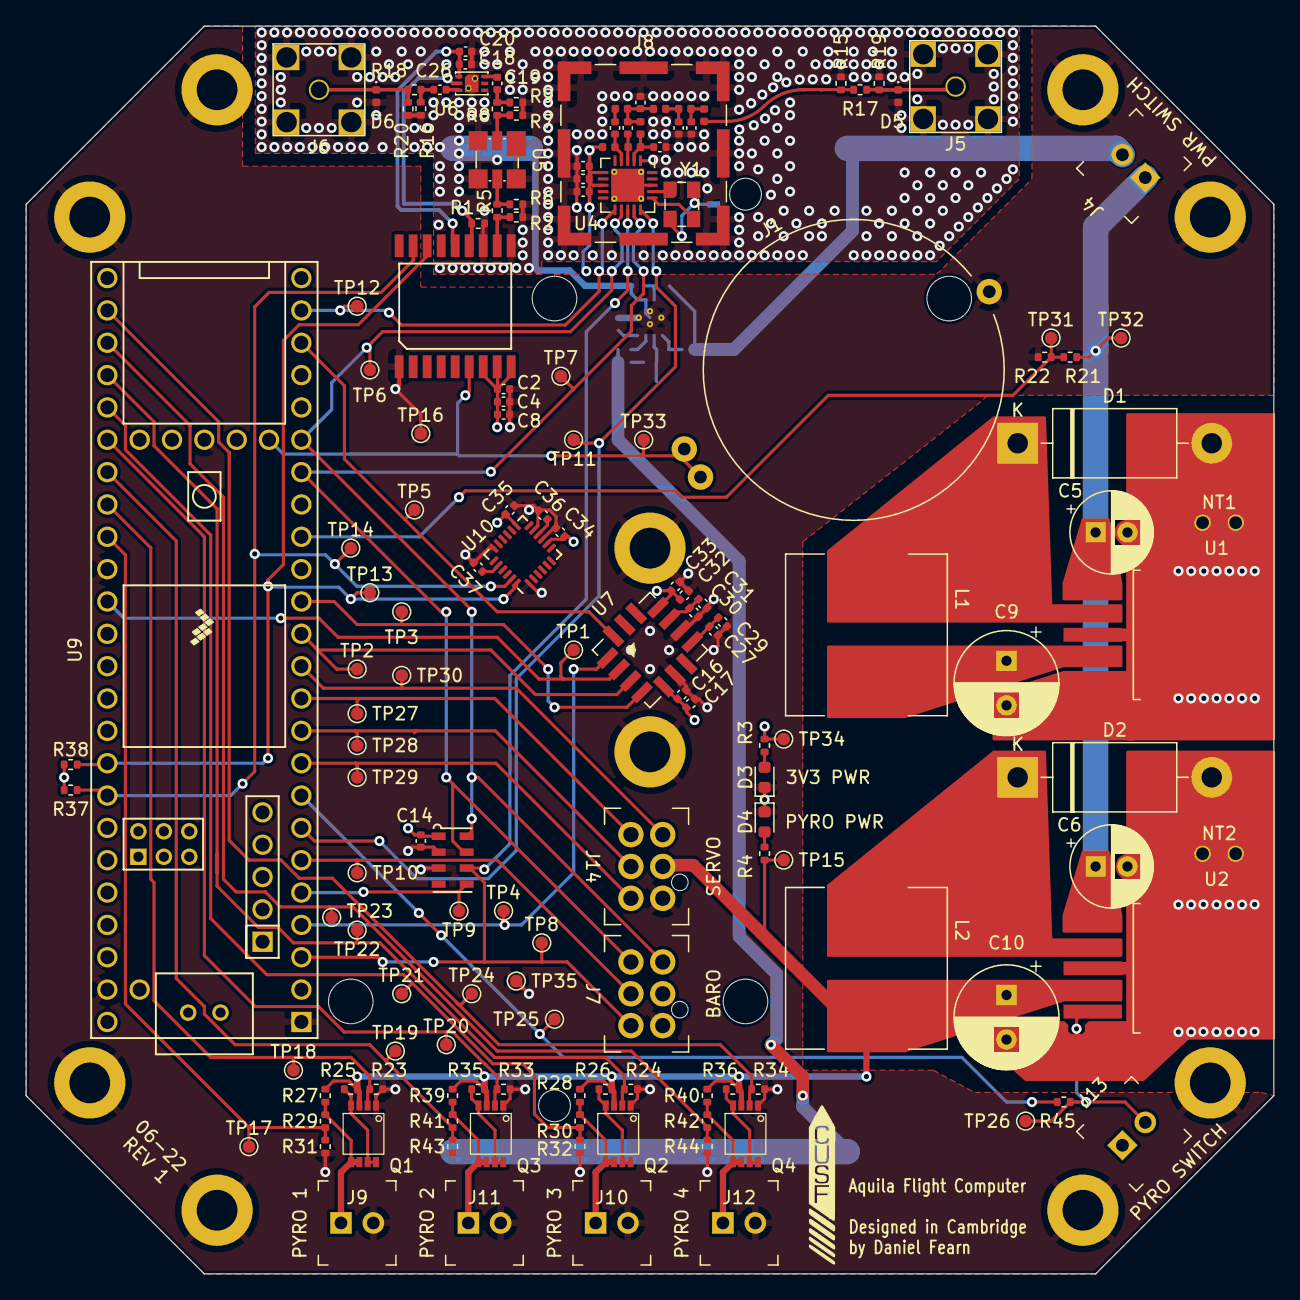
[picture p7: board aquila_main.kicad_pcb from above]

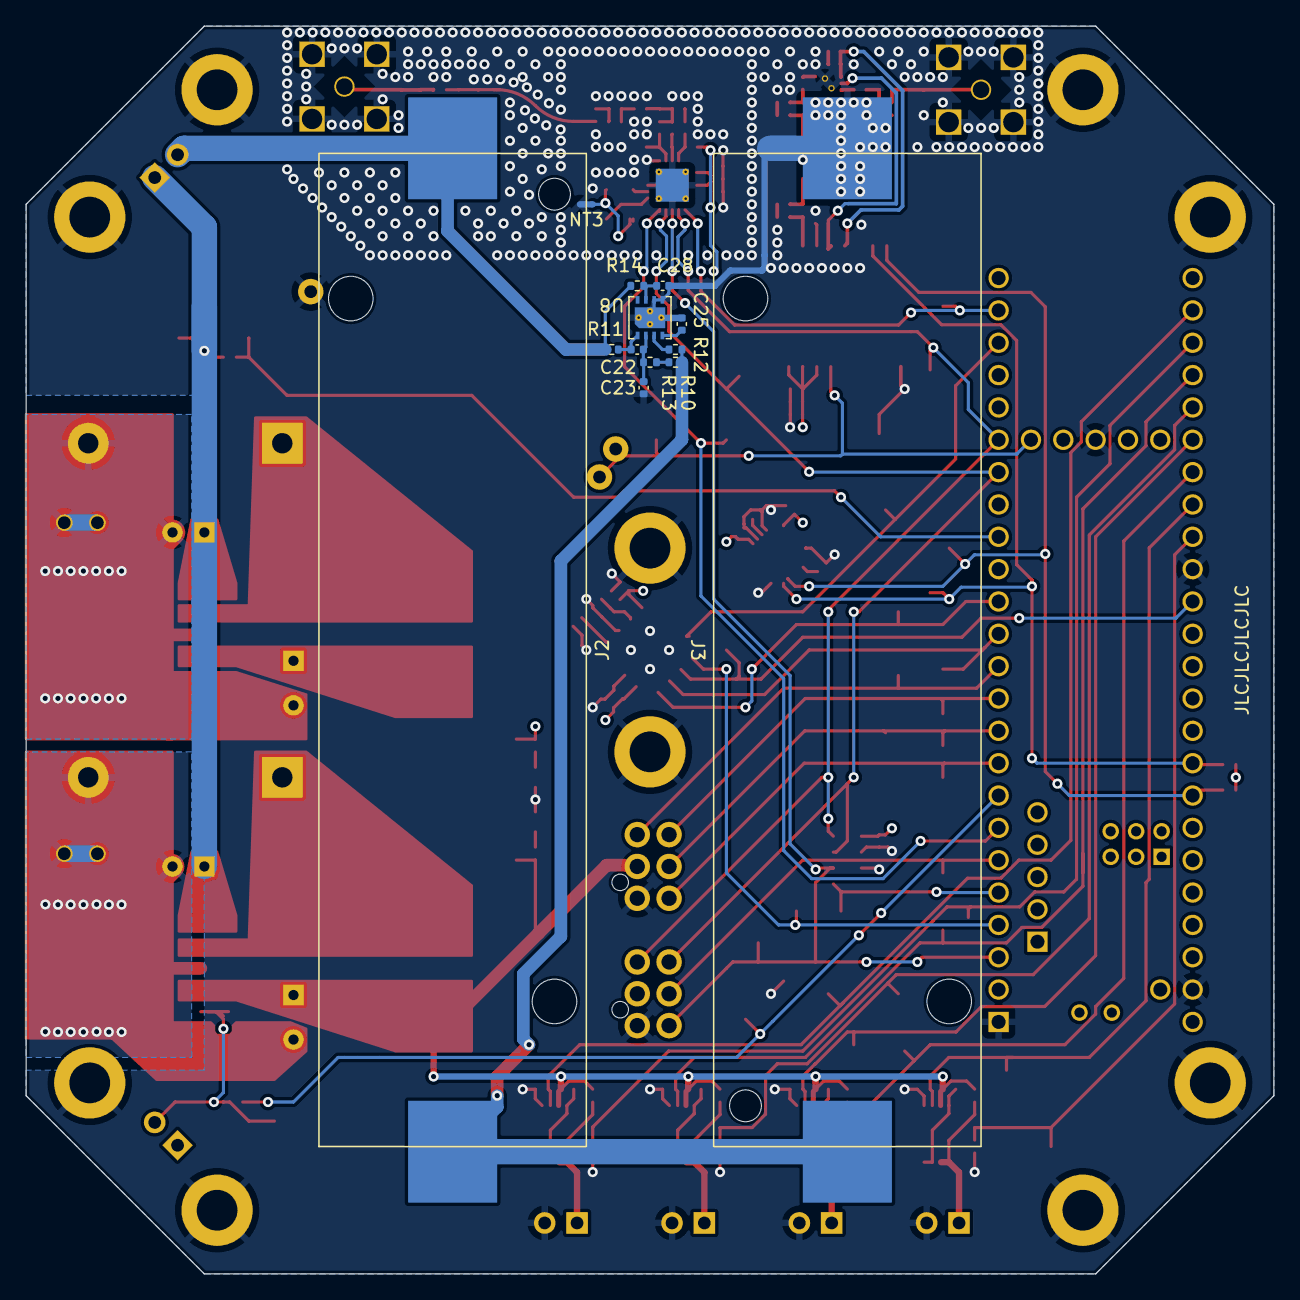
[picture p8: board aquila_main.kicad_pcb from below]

Board: 4 copper layers, 98.0 x 98.0 mm, 175 parts (13 on the bottom side), 82 nets.

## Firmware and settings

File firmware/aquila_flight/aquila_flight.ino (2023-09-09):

/* Daniel Fearn
 *  09/10/22
 *  
 *  This will be the flight program running on the Aquila-only test flight.
 *  
 * 
 */



#define pin_accel_int 30
//#define HIL_mode // uncomment to run HIL simulation of flight

#include <SD.h>

#ifdef HIL_mode
  #include <aquila_hil_interface.h>
  AQUILA_HIL aquila;
#else
  #include <aquila_interface.h>
  AQUILA aquila;
#endif


// flight state variables 
// REQ[1]
enum FlightState {LOCKED, PAD, BURN, COAST, APOGEE, DESCENT, LAND};
const char *StateNames[] = {"LOCKED", "PAD", "BURN", "COAST", "APOGEE", "DESCENT", "LAND"};
#ifdef HIL_mode
  FlightState state = PAD;
#else
  FlightState state = LOCKED; // REQ[2]
#endif
FlightState prevState = state;

// whether system parameters are being printed to serial when on the pad 
bool printing_params = false; // REQ[37][38]

// structure for encoding flight parameters for telemetry
struct FlightParams {
  uint32_t unix_time;
  byte flight_state;
  float accel_x;
  float accel_y;
  float accel_z;

  float int_pressure;
  float int_temperature;

  float imu_accel_x;
  float imu_accel_y;
  float imu_accel_z;
  float imu_gyro_x;
  float imu_gyro_y;
  float imu_gyro_z;

  float est_altitude;
  float est_velocity;

};

// timers for 10Hz and 100Hz loops
uint32_t hz10_time; // REQ[27][28]
uint32_t hz100_time; // REQ[25][26][29]
uint32_t curr_time;

// system parameters
// REQ[41]
constexpr uint8_t servo_unlocked = 0; 
constexpr uint8_t servo_locked = 70;
uint8_t servo_pos = servo_locked;
// REQ[7]
float parachute_altitude = 500; // m

// REQ[32][34][49]
float pad_pressure = 1020;

// REQ[8]
constexpr uint8_t baro_num_samples = 10; // number of samples to store
constexpr uint16_t baro_sample_period = 100; // number of 100hz loops between samples
uint16_t baro_sample_count = 0; // counts 100hz loops to know when to take samples
uint16_t baro_sample_index = 0; // the index in which to store the next sample
float baro_samples[baro_num_samples]; // array to store the samples

// REQ[52]
char last_cmd = '0';

// data logging
// REQ[32]
File datafile;

// altitude and velocity
// REQ[30]
volatile float altitude = 0;
volatile float velocity = 0;
volatile float acceleration = 0;
volatile uint32_t last_integ_micros = 0;
float g_cal = 9.81; // g used for acceloremeter calibration
float g_local = 9.81; // constant for low altitude, must computed at high altitudes. Mid latitude value used

void setup() {
  Serial.begin(19200);
  aquila.begin();
  aquila.move_all_servos(servo_locked);

  // REQ[30]
  pinMode(pin_accel_int, INPUT);
  attachInterrupt(digitalPinToInterrupt(pin_accel_int), accel_integration, RISING);

  // REQ[32]
  if(!SD.begin(BUILTIN_SDCARD)){
    Serial.println("Critical SD card error");
    while(!SD.begin(BUILTIN_SDCARD)){}
  }
  //SD.remove("aquila_log.csv");
  datafile = SD.open("aquila_log.csv", FILE_WRITE);
  datafile.seek(EOF);

  hz10_time = hz100_time = micros(); // REQ[25][26][27][28][29]
}

// main loop
void loop() {
  curr_time = micros();
  if (curr_time - hz10_time > 1e5) { // REQ[27][28]
    hz10_time = curr_time;
    hz10();
  }
  if (curr_time - hz100_time > 1e4) { // REQ[25][26][29]
    hz100_time = curr_time;
    hz100();
  }
}

byte loop_count = 0; // REQ[33][52]
// things to do at 10Hz
// REQ[27][28]
void hz10(){
  uint32_t loop_time = micros();
  if (printing_params /*& (state == LOCKED || state == PAD)*/){print_serial_state();}

  // every other loop either check if a command is received, or send a packet.
  // can't do both bc of async timing of the radio REQ[21][33][52]
  loop_count++;
  if (loop_count & 0b00000001) {
    handle_radio_command();
    send_telemetry();
  } else {
    aquila.start_listening();
  }

  // REQ[11]
  if (state == LAND) {
    // REQ[32]
    log_sd_state(loop_time);
  }
}

// things to do at 100Hz
// REQ[25][26][29]
void hz100(){
  uint32_t loop_time = micros();
  // REQ[31]
  aquila.update_imu();
  aquila.poll_baro_int();

  // REQ[11]
  if (state != LAND) {
    // REQ[32]
    log_sd_state(loop_time);
  }

  // state switching
  switch(state) {
    case LOCKED:
      handle_serial_command(); // REQ[35][23]
      break;
    case PAD:
      handle_serial_command(); // REQ[35][23]
      if (velocity > 0.5) {state = BURN;} // REQ[4]
      break;
    case BURN:
      if (acceleration < 0) {state = COAST;} // REQ[5]
      break;
    case COAST:
      if (velocity < 0) {state = APOGEE;} // REQ[6]
      break;
    case APOGEE:
      if (abs_altitude(aquila.get_int_pressure(), pad_pressure) < parachute_altitude) {state = DESCENT;} // REQ[7]
      break;
    case DESCENT:
      // REQ[8]
      if (++baro_sample_count > baro_sample_period) {
        baro_sample_count = 0;
        if (++baro_sample_index > baro_num_samples) {baro_sample_index = 0;}
        baro_samples[baro_sample_index] = aquila.get_int_pressure();

        if (abs(baro_samples[baro_sample_index]-baro_samples[ (baro_sample_index+1)%baro_num_samples ]) < 1 ) {
          state = LAND;
        }
      }

      

      break;
    case LAND:

      break;
  }
  
  // state entry actions
  if (state != prevState) {
    switch (state) {
      case LOCKED: // REQ[46]
        altitude = 0;
        velocity = 0;
        last_integ_micros = 0;
        break;
      case APOGEE: // REQ[9]
        // deploy nosecone
        safely_arm_pyro();
        aquila.fire_pyro(1);
        aquila.fire_pyro(2);
        aquila.fire_pyro(3);
        aquila.fire_pyro(4);
        break;
      case DESCENT: // REQ[10]
        // deploy parachutes
        servo_pos = servo_unlocked;
        aquila.move_all_servos(servo_pos);
        break;

      case LAND: // REQ[51]
        aquila.disarm_pyro();
        break;

      default:
        break;
    }
  }
  prevState = state;
}

// REQ[52]
void handle_radio_command(){
  char cmd = '0';
  aquila.receive_telec((char*)&cmd);
  if (cmd != '0' && cmd != last_cmd) {
    execute_command(cmd);
    last_cmd = cmd;
  }
}

// reads and performs single character commands from Serial. All characters after the first are discarded.
// REQ[35]
void handle_serial_command(){
  if (Serial.available() == 0){ return; }

  // read first character
  char cmd = Serial.read();

  // empty buffer of any other characters
  while (Serial.available() > 0){Serial.read();}

  execute_command(cmd);

}

void execute_command(char cmd) {
  if (cmd == 'N') { // REQ[36]
    print_serial_state();
  } else if (cmd == 'S') { // REQ[37]
    printing_params = true;
  } else if (cmd == 'P') { // REQ[38]
    printing_params = false;
  } else if (cmd == 'L') { // REQ[39]
    state = LOCKED; // REQ[45]
  } else if (cmd == 'U') { // REQ[40]
    state = PAD; // REQ[3]
  } else if (cmd == 'V') { // REQ[41]
    if (state == LOCKED && aquila.pyro_is_armed()) { // REQ[44]
      servo_pos = (servo_pos == servo_unlocked) ? servo_locked : servo_unlocked;
      aquila.move_all_servos(servo_pos);
    }
  } else if (cmd == 'A') { // REQ[42]
    safely_arm_pyro();

  } else if (cmd == 'D') { // REQ[43]
    aquila.disarm_pyro();
  } else if (cmd == 'C') { // REQ[49]
    pad_pressure = aquila.get_int_pressure();
  }
}

// prints timestamp, all sensor values to serial
// REQ[34][36][37][38]
void print_serial_state(){
  char timestamp[32];
  aquila.rtc_datetime(timestamp);
  Serial.println(timestamp);

  Serial.print("State: ");
  Serial.println(StateNames[state]);

  Serial.print("Accelerations (ADXL357): ");
  Serial.print(aquila.get_accel_x(), 4);
  Serial.print(", ");
  Serial.print(aquila.get_accel_y(), 4);
  Serial.print(", ");
  Serial.println(aquila.get_accel_z(), 4);

  Serial.print("Accelerations (MPU6050): ");
  Serial.print(aquila.get_imu_accel_x(), 4);
  Serial.print(", ");
  Serial.print(aquila.get_imu_accel_y(), 4);
  Serial.print(", ");
  Serial.println(aquila.get_imu_accel_z(), 4);

  Serial.print("Gyroscopes: ");
  Serial.print(aquila.get_imu_gyro_x(), 4);
  Serial.print(", ");
  Serial.print(aquila.get_imu_gyro_y(), 4);
  Serial.print(", ");
  Serial.println(aquila.get_imu_gyro_z(), 4);
  
  Serial.print("Internal barometer: ");
  Serial.print(aquila.get_int_temperature());
  Serial.print(", ");
  Serial.print(aquila.get_int_pressure());
  Serial.print(", ");
  Serial.println(abs_altitude(aquila.get_int_pressure(), pad_pressure));

  Serial.print("Battery voltage: ");
  Serial.println(aquila.get_batt_voltage());

  Serial.print("Pyro armed: ");
  Serial.println(aquila.pyro_is_armed());

  Serial.print("Pyro continuities: ");
  if (aquila.pyro_is_armed()){
    Serial.print(aquila.pyro_continuity(1));
    Serial.print(", ");
    Serial.print(aquila.pyro_continuity(2));
    Serial.print(", ");
    Serial.print(aquila.pyro_continuity(3));
    Serial.print(", ");
    Serial.println(aquila.pyro_continuity(4));
  } else {
    Serial.println("pyrotechnics must be armed to test continuity");
  }

  Serial.print("Servo position: ");
  Serial.println((servo_pos == servo_locked) ? "LOCKED" : "RELEASE");

  Serial.print("Velocity estimate: ");
  Serial.println(velocity, 4);
  Serial.print("Altitude estimate: ");
  Serial.println(altitude, 4);

  for (uint8_t i = 0; i < baro_num_samples; i++) {
    Serial.print(baro_samples[i]);
    Serial.print(",");
  }
  Serial.println();

  Serial.println();
}

// prints all data to a line in the SD file
void log_sd_state(uint32_t loop_time){

  // time
  char time[21];
  snprintf_P(time, sizeof(time), PSTR("%i,%i"), aquila.rtc_unix(), loop_time);
  // velocity/altitude estimates
  char alt[12]; // 4 dp + point + 6 digits + minus sign = 12
  char vel[12];
  dtostrf(altitude, 1, 4, alt);
  dtostrf(velocity, 1, 4, vel);
  // ADXL357
  char ax[9]; // 5 dp + p + 2 digits + minus sign = 9
  char ay[9];
  char az[9];
  dtostrf(aquila.get_accel_x(), 1, 5, ax);
  dtostrf(aquila.get_accel_y(), 1, 5, ay);
  dtostrf(aquila.get_accel_z(), 1, 5, az);
  // MPU6050
  char mp_ax[8]; // 4 dp + p + 2 digits + minus sign = 8
  char mp_ay[8];
  char mp_az[8];
  dtostrf(aquila.get_imu_accel_x(), 1, 4, mp_ax);
  dtostrf(aquila.get_imu_accel_y(), 1, 4, mp_ay);
  dtostrf(aquila.get_imu_accel_z(), 1, 4, mp_az);
  char mp_gx[8]; // 2 dp + p + 4 digits + minus sign = 8
  char mp_gy[8];
  char mp_gz[8];
  dtostrf(aquila.get_imu_gyro_x(), 1, 2, mp_gx);
  dtostrf(aquila.get_imu_gyro_y(), 1, 2, mp_gy);
  dtostrf(aquila.get_imu_gyro_z(), 1, 2, mp_gz);
  // Internal barometer
  char int_t[6]; // 2 dp + p + 2 digits + minus sign = 6
  char int_p[7]; // 2 dp + p + 4 digits = 7
  dtostrf(aquila.get_int_temperature(), 1, 2, int_t);
  dtostrf(aquila.get_int_pressure(), 1, 2, int_p);
  // Battery voltage
  char b_v[5]; // 2 dp + p + 1 digit + minus sign = 5
  dtostrf(aquila.get_batt_voltage(), 1, 2, b_v);
  // Pyros
  char rec[14]; // 5 bools + 3 digits + 6 commas = 14
  snprintf_P(rec, sizeof(rec), PSTR("%d,%d,%d,%d,%d,%i"),
    aquila.pyro_is_armed(),
    aquila.pyro_continuity(1),
    aquila.pyro_continuity(2),
    aquila.pyro_continuity(3),
    aquila.pyro_continuity(4),
    servo_pos
  );
  

  
  char line[168];
  snprintf_P(line, sizeof(line), PSTR("%s,%s,%s,%s,%s,%s,%s,%s,%s,%s,%s,%s,%s,%s,%s,%s,%s"), 
            time, StateNames[state], 
            vel, alt, ax, ay, az, 
            mp_ax, mp_ay, mp_az, mp_gx, mp_gy, mp_gz,
            int_t, int_p,
            b_v, rec
  );

  datafile.println(line);
  datafile.flush();
}

// handles accelerometer interrupt
// REQ[30]
void accel_integration() {
  if (state == LOCKED || state == LAND) {return;} // REQ[18]

  aquila.update_accel();

  uint32_t now = micros();
  if (last_integ_micros == 0) {
    last_integ_micros = now;
    return;
  }

  float accel = aquila.get_accel_z(); // g

  if (abs(accel - 1) < 0.01 && (state == PAD)) { // REQ[47]
    accel = 1;
  } 

  acceleration = accel * g_cal; // m/s/s

  float dt = (now - last_integ_micros)*1e-6;
  velocity += (acceleration - g_local) * dt;
  altitude += velocity * dt;

  last_integ_micros = now;

}

// roughly converts pressure reading to altitude
// REQ[32][34][49]
float abs_altitude(float pressure, float sea_level) {
  return 44330*(1-pow((pressure/sea_level), (1/5.255)));
}

// arms pyro channels with safeguards
// REQ[48]
void safely_arm_pyro() {
  servo_pos = servo_locked;
  aquila.move_all_servos(servo_pos);
  aquila.arm_pyro();
}

// REQ[33]
void send_telemetry() {
  FlightParams data;

  byte flight_state = (state & 0b00000111)
   + (aquila.pyro_continuity(1) << 6)
   + (aquila.pyro_continuity(2) << 5)
   + (aquila.pyro_continuity(3) << 4)
   + (aquila.pyro_continuity(4) << 3)
   + (aquila.pyro_is_armed() << 7);

  data.unix_time = micros();
  data.flight_state = flight_state;
  data.accel_x = aquila.get_accel_x();
  data.accel_y = aquila.get_accel_y();
  data.accel_z = aquila.get_accel_z();
  data.int_pressure = aquila.get_int_pressure();
  data.int_temperature = aquila.get_int_temperature();

  data.imu_accel_x = aquila.get_imu_accel_x();
  data.imu_accel_y = aquila.get_imu_accel_y();
  data.imu_accel_z = aquila.get_imu_accel_z();
  data.imu_gyro_x = aquila.get_imu_gyro_x();
  data.imu_gyro_y = aquila.get_imu_gyro_y();
  data.imu_gyro_z = aquila.get_imu_gyro_z();

  data.est_altitude = altitude;
  data.est_velocity = velocity;

  aquila.transmit_telem((uint8_t)(sizeof data), (char*)&data);
  
}

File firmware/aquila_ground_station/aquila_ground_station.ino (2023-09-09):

#include "Arduino.h"
#include "SPI.h"

#include "rfm95w.h"

RFM95W radio;

enum FlightState {LOCKED, PAD, BURN, COAST, APOGEE, DESCENT, LAND};
const char *StateNames[] = {"LOCKED", "PAD", "BURN", "COAST", "APOGEE", "DESCENT", "LAND"};

bool humanReadable = false; // whether to send serial data in csv or human readable form

struct FlightParams {
  uint32_t unix_time;
  byte  flight_state;
  float accel_x;
  float accel_y;
  float accel_z;

  float int_pressure;
  float int_temperature;

  float imu_accel_x;
  float imu_accel_y;
  float imu_accel_z;
  float imu_gyro_x;
  float imu_gyro_y;
  float imu_gyro_z;

  float est_altitude;
  float est_velocity;

};

FlightParams data;
FlightParams oldData;

void setup(){
    Serial.begin(19200);

    radio.begin(4);
    radio.init_receive();
}

void loop(){
    // telecommand
    if (Serial.available() != 0){

      char cmd = Serial.read();

      while (Serial.available() > 0){Serial.read();}

      if (cmd == ';') {
        humanReadable = false;
      } else if (cmd == '?') {
        humanReadable = true;
      } else {
        if (humanReadable) {
          Serial.print("\n\nSending command: ");
          Serial.println(cmd);
          Serial.println("\n");
        }

        for (int i = 0; i < 20; i++) {
          radio.transmit(1, &cmd);
          delay(20);
        }
        radio.init_receive();
      }

    }

    // telemetry
    radio.check_received((char*)&data, 64);

    // compare an arbitrary but noisey value to see if its changed
    if (data.imu_accel_y != oldData.imu_accel_y) {
      if (humanReadable) {
        // human readable format
        Serial.println(data.unix_time);

        Serial.print("State: ");
        Serial.println(StateNames[(data.flight_state & 0b00000111)]);

        Serial.print("Accelerations (ADXL357): ");
        Serial.print(data.accel_x, 4);
        Serial.print(", ");
        Serial.print(data.accel_y, 4);
        Serial.print(", ");
        Serial.println(data.accel_z, 4);

        Serial.print("Accelerations (MPU6050): ");
        Serial.print(data.imu_accel_x, 4);
        Serial.print(", ");
        Serial.print(data.imu_accel_y, 4);
        Serial.print(", ");
        Serial.println(data.imu_accel_z, 4);

        Serial.print("Pyro armed: ");
        Serial.println(data.flight_state >> 7);
        Serial.print("Pyro continuities: ");
        Serial.print((data.flight_state & 0b01000000) >> 6);
        Serial.print(", ");
        Serial.print((data.flight_state & 0b00100000) >> 5);
        Serial.print(", ");
        Serial.print((data.flight_state & 0b00010000) >> 4);
        Serial.print(", ");
        Serial.println((data.flight_state & 0b00001000) >> 3);

        Serial.print("Gyroscopes: ");
        Serial.print(data.imu_gyro_x, 4);
        Serial.print(", ");
        Serial.print(data.imu_gyro_y, 4);
        Serial.print(", ");
        Serial.println(data.imu_gyro_z, 4);
        
        Serial.print("Internal barometer: ");
        Serial.print(data.int_pressure);
        Serial.print(", ");
        Serial.println(data.int_temperature);

        Serial.print("Velocity estimate: ");
        Serial.println(data.est_velocity, 4);
        Serial.print("Altitude estimate: ");
        Serial.println(data.est_altitude, 4);

        Serial.println();
        Serial.println();
      } else {
        // csv format
        Serial.print(data.unix_time);

        Serial.print(",");
        Serial.print(data.flight_state & 0b00000111);

        Serial.print(",");
        Serial.print(data.accel_x, 4);
        Serial.print(",");
        Serial.print(data.accel_y, 4);
        Serial.print(",");
        Serial.print(data.accel_z, 4);

        Serial.print(",");
        Serial.print(data.imu_accel_x, 4);
        Serial.print(",");
        Serial.print(data.imu_accel_y, 4);
        Serial.print(",");
        Serial.print(data.imu_accel_z, 4);

        Serial.print(",");
        Serial.print(data.flight_state >> 7);
        Serial.print(",");
        Serial.print((data.flight_state & 0b01000000) >> 6);
        Serial.print(",");
        Serial.print((data.flight_state & 0b00100000) >> 5);
        Serial.print(",");
        Serial.print((data.flight_state & 0b00010000) >> 4);
        Serial.print(",");
        Serial.print((data.flight_state & 0b00001000) >> 3);

        Serial.print(",");
        Serial.print(data.imu_gyro_x, 4);
        Serial.print(",");
        Serial.print(data.imu_gyro_y, 4);
        Serial.print(",");
        Serial.print(data.imu_gyro_z, 4);
        
        Serial.print(",");
        Serial.print(data.int_pressure);
        Serial.print(",");
        Serial.print(data.int_temperature);

        Serial.print(",");
        Serial.print(data.est_velocity, 4);
        Serial.print(",");
        Serial.println(data.est_altitude, 4);
      }
    }

    oldData = data;

    delay(100);
}

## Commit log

2022-03-06 added symbol and footprint for ADXL357
    [aquila_main.sch]
2022-03-06 added connections for accelerometer
    [aquila_main.sch]
2022-03-10 added symbol and footprint for RTC bat. holder
    [aquila_main.sch]
2022-03-10 added connections for barometer
    [aquila_main.sch]
2022-03-11 added DXF of flange for reference
    [flange.dxf]
2022-03-12 added dimensions to flange dxf
    [flange.dxf]
2022-03-13 added connections for telemetry radio
    [aquila_main.sch]
2022-03-17 sketched potential board shape
    [flange.dxf]
2022-03-18 updated to KiCad 6
    [#flange.dxf, aquila_main.kicad_sch, aquila_main.sch]
2022-03-19 added connections for GPS
    [aquila_main.kicad_sch]
2022-03-19 added power indicator LEDs
    [aquila_main.kicad_sch]
2022-03-20 removed dependence on deprecated symbol library
    [aquila_main.kicad_sch]
2022-03-21 added battery holders and balancer
    [aquila_main.kicad_sch]
2022-03-28 added telemetry radio matching network
    [aquila_main.kicad_sch]
2022-03-28 fixed net label formatting
    [aquila_main.kicad_sch]
2022-03-29 added connections for Teensy uC
    [aquila_main.kicad_sch]
2022-03-29 designed out unobtainable components
    [aquila_main.kicad_sch]
2022-03-29 added connector for optional external barometer
    [aquila_main.kicad_sch]
2022-03-29 created footprint for LM2576
    [aquila_main.kicad_sch]
2022-03-29 copied in Teensy libraries
    [aquila_main.kicad_sch]
2022-03-29 created footprints for RF components
2022-03-29 added mounting holes
    [aquila_main.kicad_sch]
2022-03-29 added I2C pullups
    [aquila_main.kicad_sch]
2022-03-29 added Pi pad to telem line
    [aquila_main.kicad_sch]
2022-03-29 added footprint for BQ29200
    [aquila_main.kicad_sch]
2022-03-30 added RF shield
    [aquila_main.kicad_sch]
2022-03-31 changed to 868MHz matching on radio
    [aquila_main.kicad_sch]
2022-03-31 added pyro safety switch
    [aquila_main.kicad_sch]
2022-03-31 added footprint for crystal
    [aquila_main.kicad_sch]
2022-04-01 added order numbers and footprints to small parts
    [aquila_main.kicad_sch]
2022-04-01 changed PCB shape to make better use of space
    [#flange.dxf, flange.dxf]
2022-04-01 changed pyro power to 5V
    [aquila_main.kicad_sch]
2022-04-01 added connector for servos
    [aquila_main.kicad_sch]
2022-04-01 assigned all remaining footprints
    [aquila_main.kicad_sch]
2022-04-02 initialised PCB layout
    [aquila_main.kicad_pcb]
2022-04-02 preliminary placement of components
    [aquila_main.kicad_pcb, aquila_main.kicad_sch]
2022-04-03 placed all components and traces
    [aquila_main.kicad_pcb, aquila_main.kicad_sch]
2022-04-04 fixed relevant DRC errors
    [aquila_main.kicad_pcb]
2022-04-04 added silkscreen logo etc
    [aquila_main.kicad_pcb]
2022-04-05 minor adjustments
    [aquila_main.kicad_pcb]
2022-06-16 added test points, redesigned power supplies
    [aquila_main.kicad_pcb, aquila_main.kicad_sch]
2022-06-16 added dimensions for mounting holes
    [flange.dxf]
2022-07-28 added manufacture files and BoM
    [aquila_main.kicad_pcb, aquila_main.kicad_sch, aquila_main_rev_1_bom.xlsx]
2022-07-29 fixed mistake in bom
    [aquila_main_rev_1_bom.xlsx]
2022-07-30 designed PCB support
    [#flange.dxf, support-PartBody.stl, support.FCStd]
2022-08-28 added battery voltage measurement
2022-09-12 added inertial sensor calibration program
2022-10-09 removed debugging printing
2022-10-09 implemented servo control
2022-10-10 added accel interrupt handler
2022-10-11 set servo positions
2022-10-26 fixed barometer timing bug
    [aquila_interface.h, ms56_11_07.cpp]
2022-10-26 moved logging time to before reading sensors
2022-11-06 added two point calibration for mpu6050 sensor
2023-02-05 added landing detection
2023-02-19 included files for generating HIL tests
    [flight_data.csv]
2023-02-20 Added comments and corrections
    [rfm95w.cpp]
2023-08-13 tracked down SD logging bug that was causing crash on pyro arm
    [aquila_flight.ino, aquila_interface.cpp]
2023-08-13 added command to calibrate altimeter
2023-08-13 added pyro disarm on landing
2023-08-13 stop integrating on landing
2023-09-03 fixed pyro firing bug
    [aquila_interface.cpp]
2023-09-03 designed mounting hardware for LoRa module
    [rfm95w_mount-base.g, rfm95w_mount-base.stl, rfm95w_mount-top.g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]
2023-09-09 created GUI program for ground station
2023-09-09 tweaked ground station firmware to work with GUI program
2023-09-18 removed gcode
    [rfm95w_mount-base.g]
2023-09-18 removed last gcode
    [rfm95w_mount-top.g]
